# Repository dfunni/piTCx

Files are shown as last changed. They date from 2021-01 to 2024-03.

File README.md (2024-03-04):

# piTCx
piTCx is a Raspberry Pi based roaster control system using Artisan Roasterscope as front-end UI. A Raspberry Pi can interface with the piTCx Power HAT+ to record temperatures from up to four thermocouples as well as the temperature sensor (MCP9800) on the piTCx board. For roaster control, the Raspberry Pi can perform heater control using slow PWM (1 Hz) with the Artisan software providing PID control. Heater control requires a solid state relay connected to the OT1 jumper on the piTCx HAT+. The piTCx Power HAT+ can also power the host Raspberry Pi over GPIO through the 5V jumper connection.

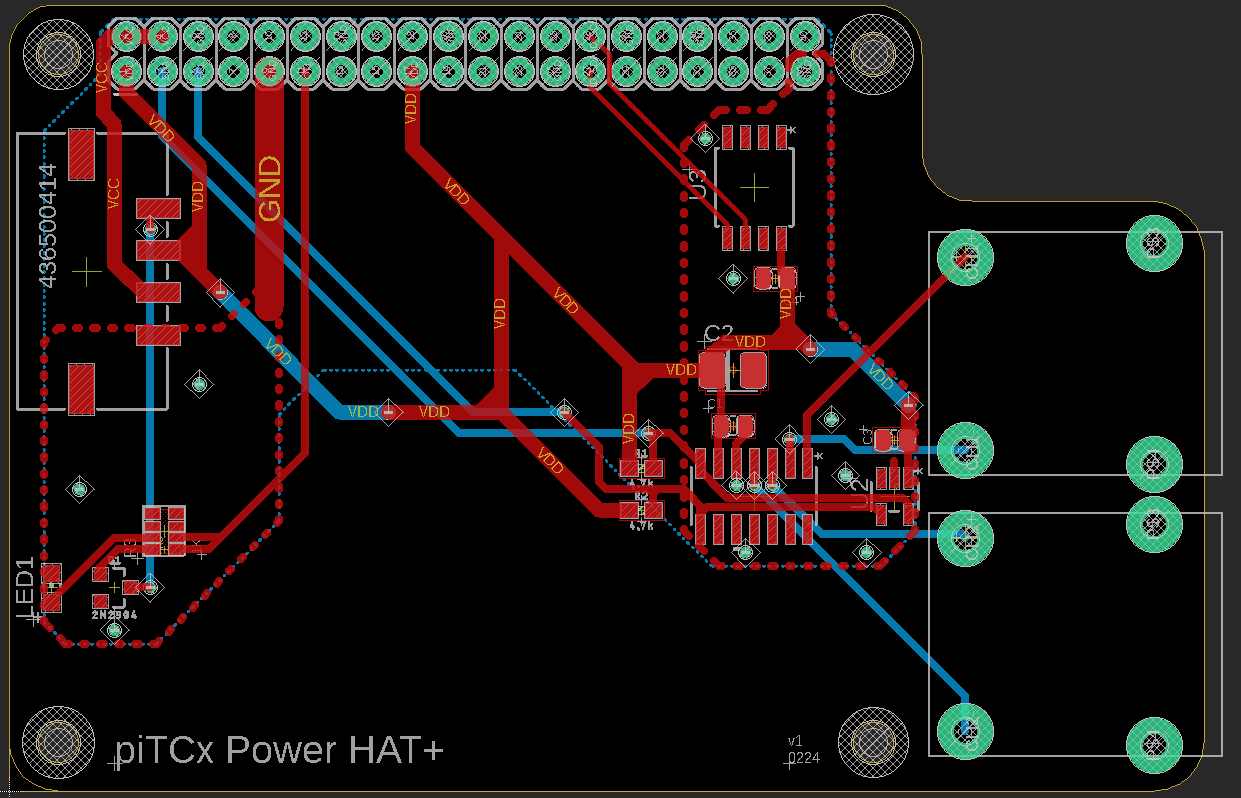
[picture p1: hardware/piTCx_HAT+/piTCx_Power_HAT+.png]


# piRoast Power
The piRoast Power is a complementary board provides  5V power to supply the Raspberry Pi via the piTCx Power HAT+. Additionally, the board contains a solid state relay for heater control.

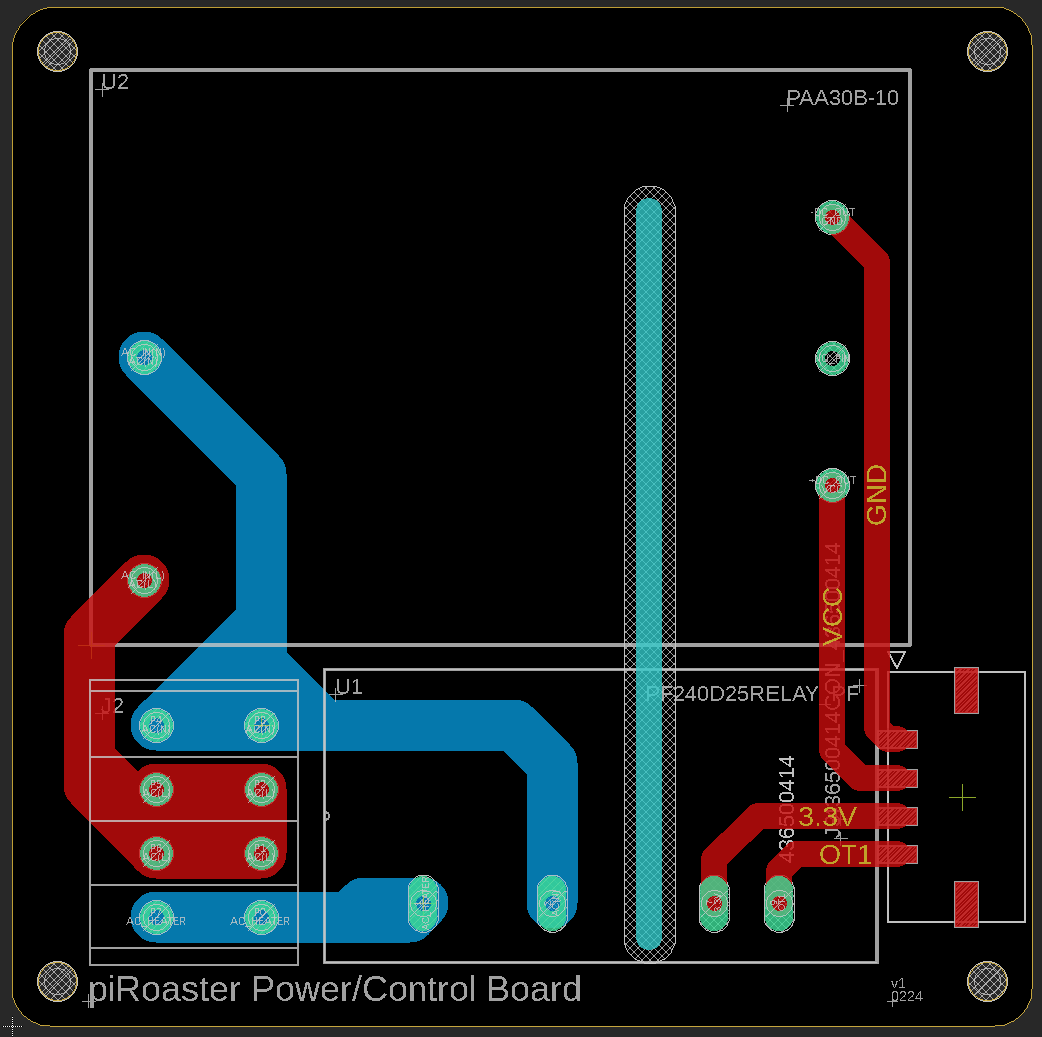
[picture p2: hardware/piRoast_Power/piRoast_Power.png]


# Raspberry Pi Setup
Starting with a fresh install of the latest raspbian OS (tested with Bookworm):

1. configure the raspi with
```
sudo raspi-config
```    
In the "Advanced" menu, select expand filesystem.

In the "Interfaces" menu enable ssh, I2C, Serial Port, and Remote GPIO.

Reboot to finish the configuration.

2. Install required tools
```
sudo apt install socat
```
3. Ensure pigpiod is enabled and running
```
sudo systemctl enable pigpiod
sudo systemctl start pigpiod
```
4. Install Artisan
```
curl -L -O https://github.com/artisan-roaster-scope/artisan/releases/download/<vx.xx.x>/<artisan-linux-x.xx.x.deb>
sudo dpkg -i <artisan-linux-x.x.x.deb>
```
5. Download and setup the piTCx code
```
git clone https://github.com/dfunni/piTCx.git
cd piTCx
python -m venv env
source env/bin/activate
pip install -r requirements.txt
```
6. Create systemd service to run the piTCx command interface. First update tcxd.service line 10 to the correct login user (e.g. pi). Then:
```
sudo cp tcxd.service /etc/systemd/system/
sudo systemctl enable tcxd.service
```
From here everything is setup and ready. The next steps are to configure Artisan for communication with the TCx board.

## (Optional) Launch Artisan on boot
Copy `start_artisan.sh` to `/etc/profile.d/` with:
```
sudo cp $HOME/piTCx/start_artisan.sh /etc/profile.d/
```
# Artisan Setup
1. Go to Config > Device
    - at the top of the ET/BT tab check Control, Curves: BT, LCDs: ET and BT
    - select TC4 radio button, set ET and BT channels, set AT Channel to None, deselect PID Firmware
    - in the Extra Devices tab add the following:
        ArduinoTC4_56; Label 1: Heater; Label 2: Fan; Curve 1: enable; Curve 2: enable
        ArduinoTC4_78; Label 1: SV; Label 2: Ambient; LCD 2: enable; Curve 1: enable; Curve 2: enable

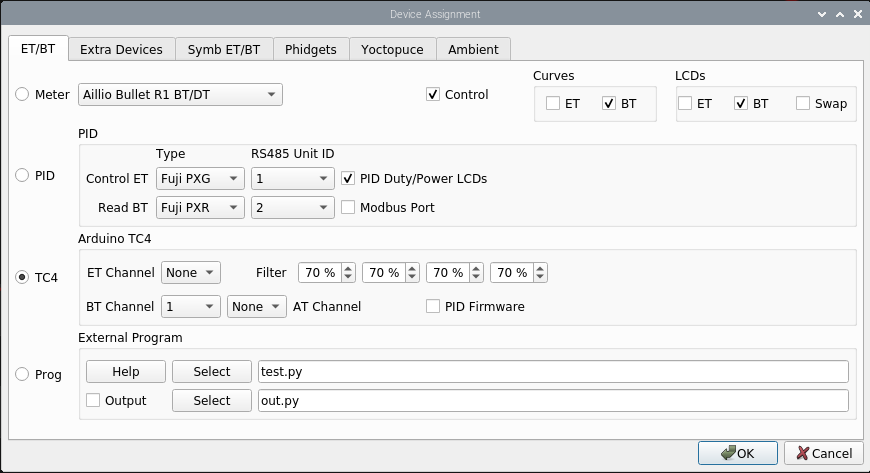
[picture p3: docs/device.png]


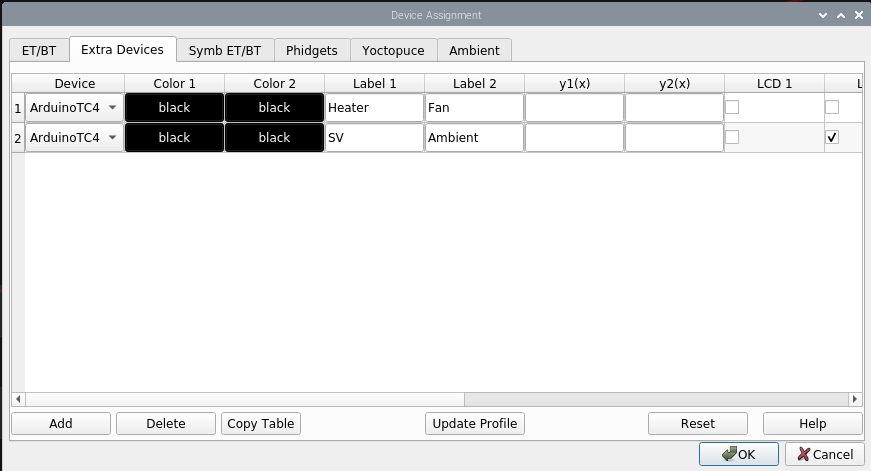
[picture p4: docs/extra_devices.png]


2. In Ports set Comm Port to /dev/ttyS91 with 115200-8-N-1 and change the serial Timeout to **0.4** seconds

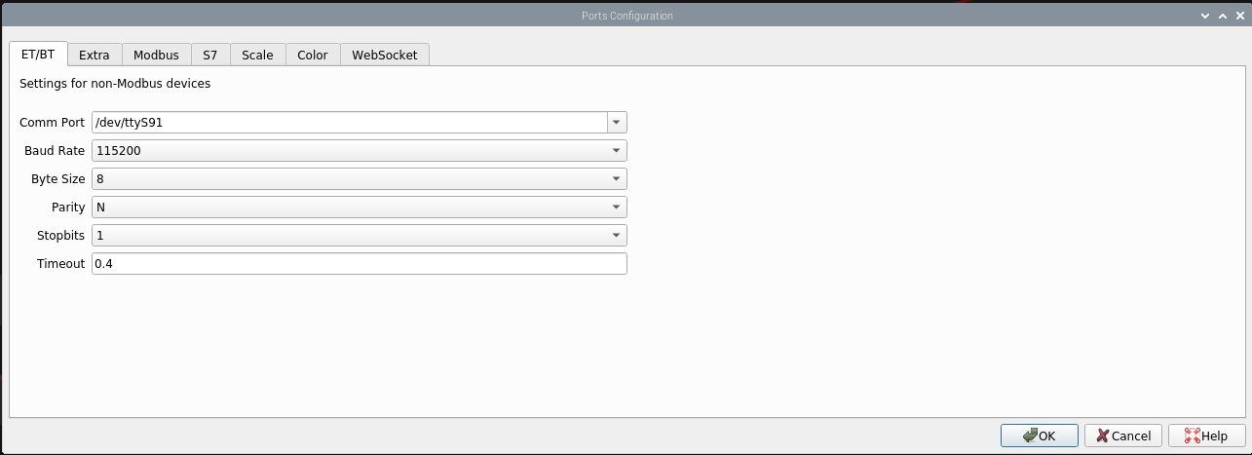
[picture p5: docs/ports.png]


3. Config > Sampling set to 1.0 seconds, accept the popup

4. Config > Curves select BT Projection and set to linear

5. Config > Events
     - set Event Types 2 to Heater and have that as the only event tyupe slected
     - set Default Buttons - DROP to Serial Command: OT1;0
     - under the Buttons Tab add the following
        Heater MAX; Type: Heater; Value: 100; Action: Serial Command; Documentation: OT1;{}
        Heater Off; Type: Heater; Value: 0; Action: Serial Command; Documentation: OT1;{}
        PID OFF; Type: Heater Value: 0; Action: Artisan Command; Documentation: PIDoff
    - Sliders - Event: Heater; Action: Serial Command; Command: OT1;{}

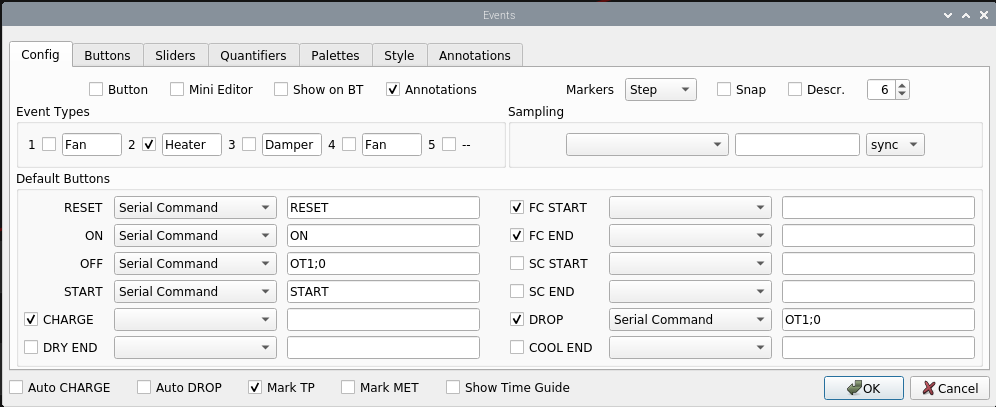
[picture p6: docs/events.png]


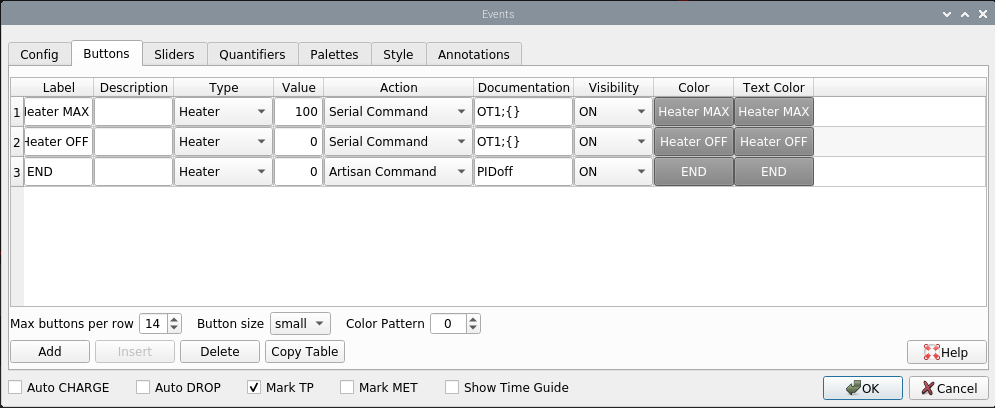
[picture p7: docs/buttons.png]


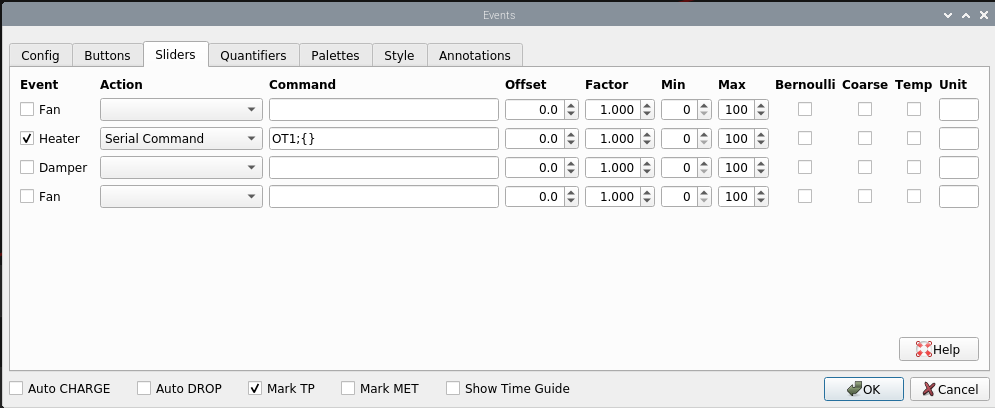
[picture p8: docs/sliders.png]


6. Config > Temperature > Celcius Mode

7. Roast > Background
    - show, BT selected
    - Load background .alog file

8. Control (Button)
    - kp: 1.30
    - ki: 0.06
    - kd: 4.50
    - Source: BT; Target - Positive: Heater; Set Value - Mode: Background; Set PID on CHARGE: enabled

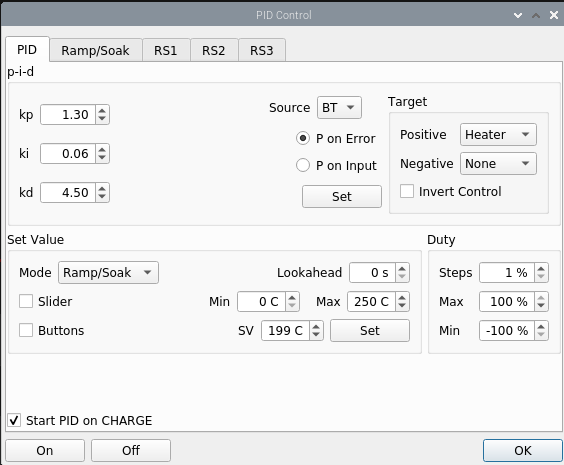
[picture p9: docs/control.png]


# Testing piTCx on Raspberry Pi
1. Ensure Raspberry Pi setup is completed per instructions in Raspberry Pi Setup
  section. Ensure piTCx HAT+ is connected.

3. In the ~/piTCx directory run pytests with:
```
cd ~/piTCx
pytest --cov
```

3. Navigate to the ~/piTCx/tests/ directory and run:
```
cd tests/
./integration_test.sh
```
Monitor the output to ensure temperatures are read, no errors are produced.

4. Run the sample rate test to ensure 1.0 second sampling intervals are working:
```
./samprate_test.sh
```
Monitor the output to esure 10 reads are taken. Check the timestamps for 1 second accuracy. 

5. Additionally, a single Artisan command can be executed with:
```
./ArtisonCMD.sh <command> [<value>]
```
 using a command value pair from the following:
| command | value | notes |
| --- | ----- | ----- |
| CHAN | 1234  | Initializes the piTCx and sets order of ADC channels |
| READ | | No value for READ command |
| UNITS | F/C | Temperature units to be read |
| OT1 | 0-100 | Sets OT1 duty cycle |
| OT2 | 0-100 | Sets OT2 duty cycle |
| IO2 | 0-100 | Sets IO2 duty cycle |

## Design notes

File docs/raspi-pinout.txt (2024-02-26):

3V3 -    3V3  (1) (2)  5V     - 5V 
SDA -  GPIO2  (3) (4)  5V     - 5V 
SCL -  GPIO3  (5) (6)  GND    - GND
--- -  GPIO4  (7) (8)  GPIO14 - ---
GND -    GND  (9) (10) GPIO15 - --- 
OT1 - GPIO17 (11) (12) GPIO18 - --- 
--- - GPIO27 (13) (14) GND    - GND
--- - GPIO22 (15) (16) GPIO23 - ---
3V3 -    3V3 (17) (18) GPIO24 - ---
--- - GPIO10 (19) (20) GND    - GND
--- -  GPIO9 (21) (22) GPIO25 - ---
--- - GPIO11 (23) (24) GPIO8  - ---
GND -    GND (25) (26) GPIO7  - ---
--- -  GPIO0 (27) (28) GPIO1  - ---
--- -  GPIO5 (29) (30) GND    - GND 
--- -  GPIO6 (31) (32) GPIO12 - ---
--- - GPIO13 (33) (34) GND    - GND 
--- - GPIO19 (35) (36) GPIO16 - ---
--- - GPIO26 (37) (38) GPIO20 - ---
GND -    GND (39) (40) GPIO21 - ---

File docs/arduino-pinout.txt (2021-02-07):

    SCL/D13  (16) (15) ~D12/MISO
        3V3  (17) (14) ~D11/MOSI
       AREF  (18) (13) ~D10       OT2
     A0/D14  (19) (12) ~D09       OT1
     A1/D15  (20) (11)  D08
     A2/D16~ (21) (10)  D07
     A3/D17~ (22) (09) ~D06
SDA  A4/D18  (23) (08) ~D05
SCL  A5/D19~ (24) (07)  D04
     A6/D20  (25) (06) ~D03       IO3
     A7/D20  (26) (05) ~D02       IO2
3v3      5V  (27) (04)  GND       GND
      RESET  (28) (03)  RESET
GND     GND  (29) (02)  RX        TX        
        VIN  (30) (01)  TX        RX

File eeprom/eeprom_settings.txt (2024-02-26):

########################################################################
# EEPROM settings text file
#
# Use eepflash tool to write to attached HAT ID EEPROM 
#
# Tools available:
#  eepmake   Parses EEPROM text file and creates binary .eep file
#  eepdump   Dumps a binary .eep file as human readable text (for debug)
#  eepflash  Write or read .eep binary image to/from HAT EEPROM
#
########################################################################

# RFC 4122 compliant UUID
product_uuid cafef870-ff07-4368-9851-c25b4d0d856a

# 16 bit product id
product_id 0x0000

# 16 bit product version
product_ver 0x0001

# ASCII vendor string  (max 255 characters)
vendor "dfunni"

# ASCII product string (max 255 characters)
product "piTCx Power HAT+"

# Which Device Tree overlay to load
dt_blob "i2c1"

custom_data "
piTCx is a Raspberry Pi based roaster control system, see https://github.com/dfunni/piTCx for details.

MIT License

Copyright (c) 2020 dfunni

Permission is hereby granted, free of charge, to any person obtaining a copy
of this software and associated documentation files (the "Software"), to deal
in the Software without restriction, including without limitation the rights
to use, copy, modify, merge, publish, distribute, sublicense, and/or sell
copies of the Software, and to permit persons to whom the Software is
furnished to do so, subject to the following conditions:

The above copyright notice and this permission notice shall be included in all
copies or substantial portions of the Software.

THE SOFTWARE IS PROVIDED "AS IS", WITHOUT WARRANTY OF ANY KIND, EXPRESS OR
IMPLIED, INCLUDING BUT NOT LIMITED TO THE WARRANTIES OF MERCHANTABILITY,
FITNESS FOR A PARTICULAR PURPOSE AND NONINFRINGEMENT. IN NO EVENT SHALL THE
AUTHORS OR COPYRIGHT HOLDERS BE LIABLE FOR ANY CLAIM, DAMAGES OR OTHER
LIABILITY, WHETHER IN AN ACTION OF CONTRACT, TORT OR OTHERWISE, ARISING FROM,
OUT OF OR IN CONNECTION WITH THE SOFTWARE OR THE USE OR OTHER DEALINGS IN THE
SOFTWARE.
\"

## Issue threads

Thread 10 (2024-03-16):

Need fan header on HAT and/or Power Board

dfunni, 2024-03-16:
Add a 4-pin fan header to board.

Threshold: provide 5V power to fan
Objective: PWM control of fan

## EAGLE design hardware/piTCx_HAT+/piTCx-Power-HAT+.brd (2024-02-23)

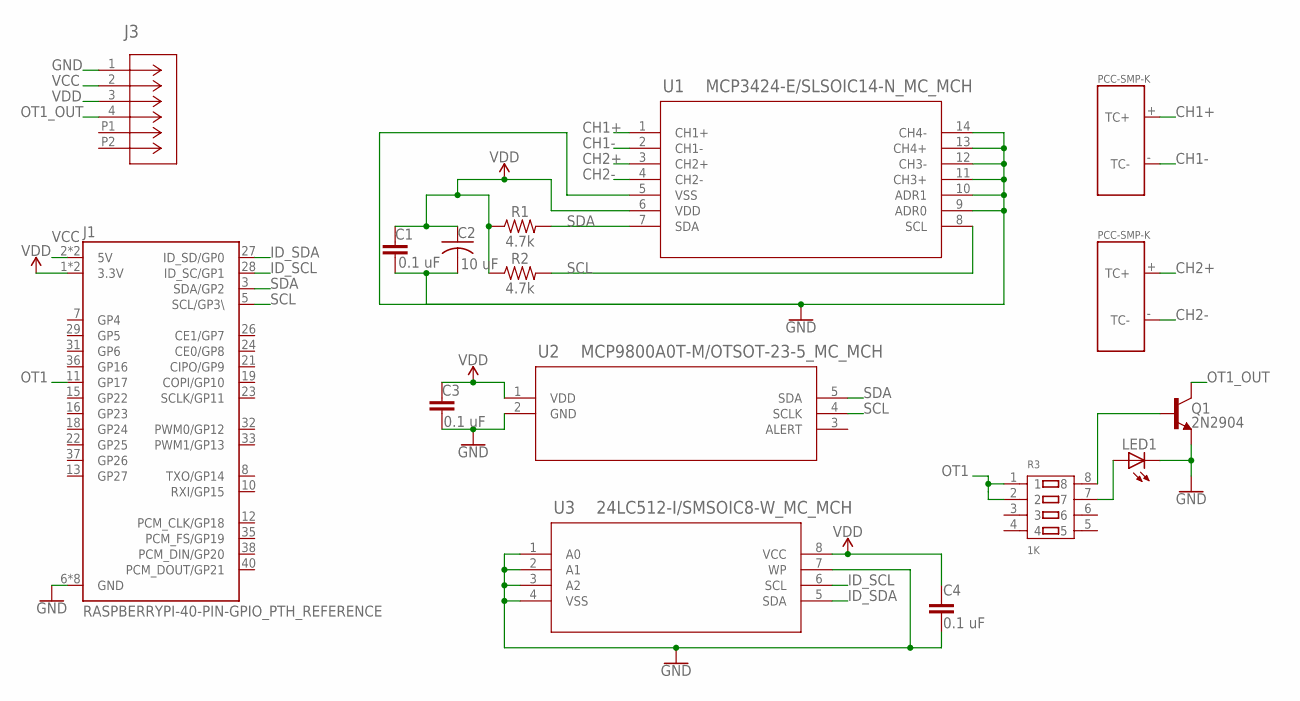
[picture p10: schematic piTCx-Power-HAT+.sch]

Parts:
C1, C3, C4: 0.1 uF; CAP_0805
C2: 10 uF; CAP_TANT_B; MPN T494A106M020AT
J1: RASPBERRYPI-40-PIN-GPIO_PTH_REFERENCE; RASPBERRY_PI_HAT_40_PIN_PTH_WITH_REFERNCE
J3: 436500414CON_436500414; CON_436500414
LED1: LEDCHIP-LED0805; CHIP-LED0805
Q1: 2N2904; SOT23-3
R1, R2: 4.7k; 0603
R3: 1K; RA1206-8
U1: MCP3424-E/SLSOIC14-N_MC_MCH; SOIC14-N_MC_MCH
U2: MCP9800A0T-M/OTSOT-23-5_MC_MCH; SOT-23-5_MC_MCH
U3: 24LC512-I/SMSOIC8-W_MC_MCH; SOIC8-W_MC_MCH
U$1, U$2: THERMOCOUPLECONN-PCC-SMP-K

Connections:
CH1+: U1.1 (CH1+), U$1.+ (TC+)
CH1-: U1.2 (CH1-), U$1.- (TC-)
CH2+: U1.3 (CH2+), U$2.+ (TC+)
CH2-: U1.4 (CH2-), U$2.- (TC-)
GND: C1.2, C2.2, C3.2, C4.2, J1.6 (GND), J1.9 (GND), J1.14 (GND), J1.20 (GND), J1.25 (GND), J1.30 (GND), J1.34 (GND), J1.39 (GND), J3.1, LED1.C, Q1.2 (E), U1.5 (VSS), U1.9 (ADR0), U1.10 (ADR1), U1.11 (CH3+), U1.12 (CH3-), U1.13 (CH4+), U1.14 (CH4-), U2.2 (GND), U3.1 (A0), U3.2 (A1), U3.3 (A2), U3.4 (VSS), U3.7 (WP)
ID_SCL: J1.28 (ID_SC/GP1), U3.6 (SCL)
ID_SDA: J1.27 (ID_SD/GP0), U3.5 (SDA)
unnamed: Q1.1 (B), R3.8
unnamed: LED1.A, R3.7
OT1: J1.11 (GP17), R3.1, R3.2
OT1_OUT: J3.4, Q1.3 (C)
SCL: J1.5 (SCL/GP3\), R2.2, U1.8 (SCL), U2.4 (SCLK)
SDA: J1.3 (SDA/GP2), R1.2, U1.7 (SDA), U2.5 (SDA)
VCC: J1.2 (5V), J1.4 (5V), J3.2
VDD: C1.1, C2.1, C3.1, C4.1, J1.1 (3.3V), J1.17 (3.3V), J3.3, R1.1, R2.1, U1.6 (VDD), U2.1 (VDD), U3.8 (VCC)

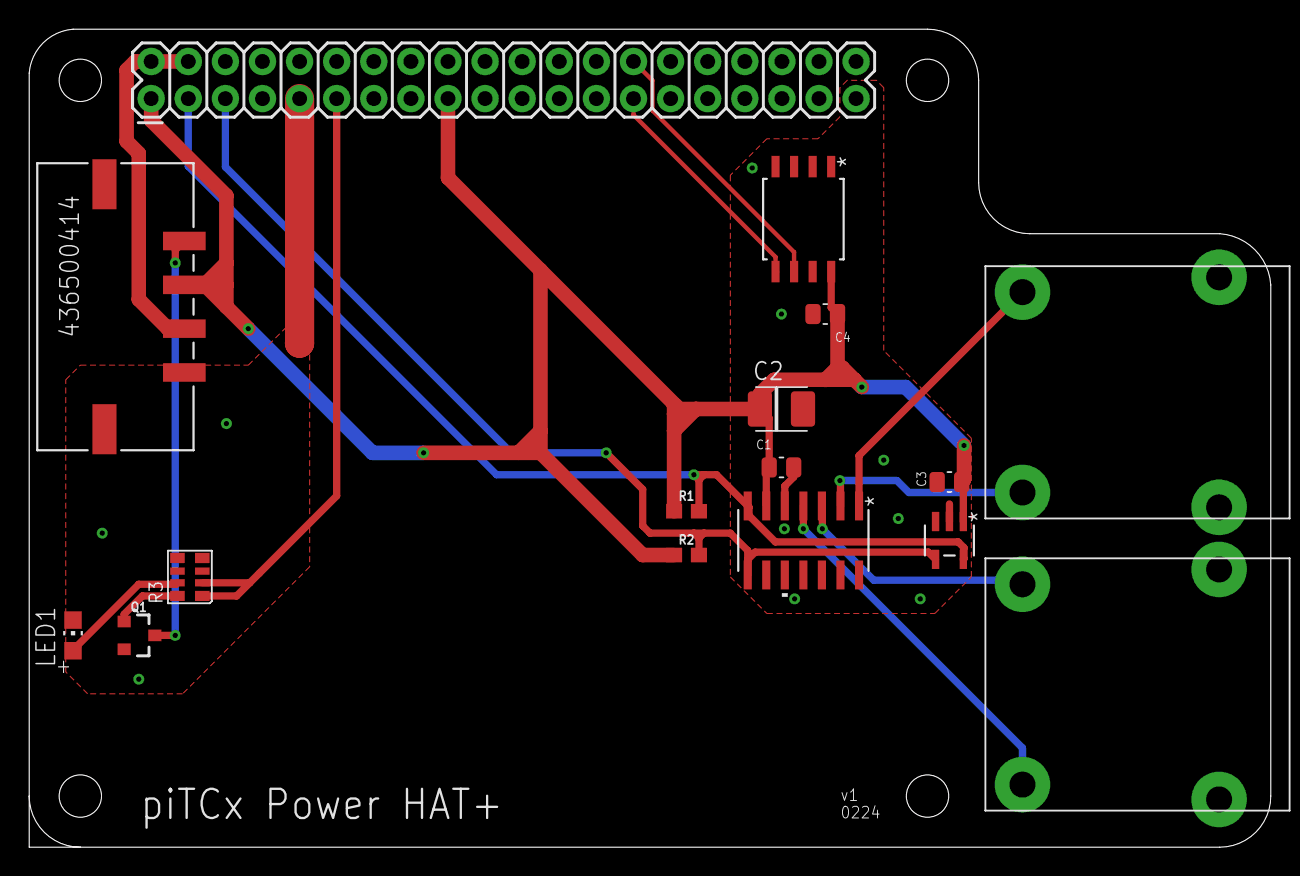
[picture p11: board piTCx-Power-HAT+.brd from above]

Board: 2 copper layers, 85.0 x 56.0 mm, 16 parts (0 on the bottom side), 15 nets.

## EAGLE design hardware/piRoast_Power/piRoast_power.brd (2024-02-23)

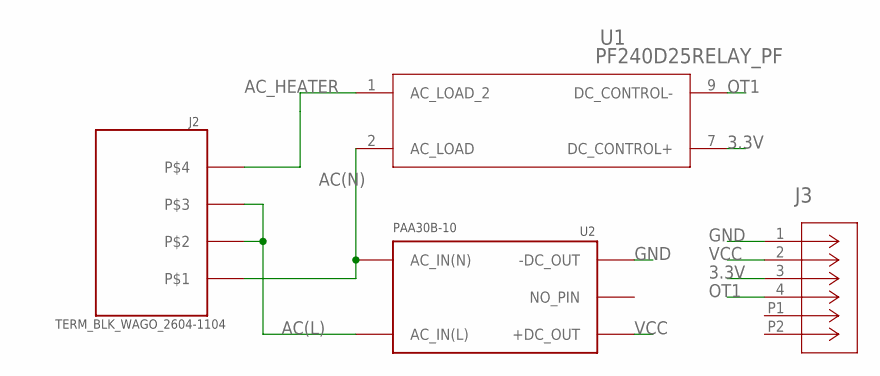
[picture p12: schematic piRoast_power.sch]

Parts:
J2: TERM_BLK_WAGO_2604-1104
J3: 436500414CON_436500414; CON_436500414
U1: PF240D25RELAY_PF; RELAY_PF
U2: PAA30B-10

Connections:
3.3V: J3.3, U1.7 (DC_CONTROL+)
AC(L): J2.P1, J2.P2, J2.P5, J2.P6, U2.AC_IN(L)
AC(N): J2.P3, J2.P4, U1.2 (AC_LOAD), U2.AC_IN(N)
AC_HEATER: J2.P0, J2.P7, U1.1 (AC_LOAD_2)
GND: J3.1, U2.-DC_OUT
OT1: J3.4, U1.9 (DC_CONTROL-)
VCC: J3.2, U2.+DC_OUT

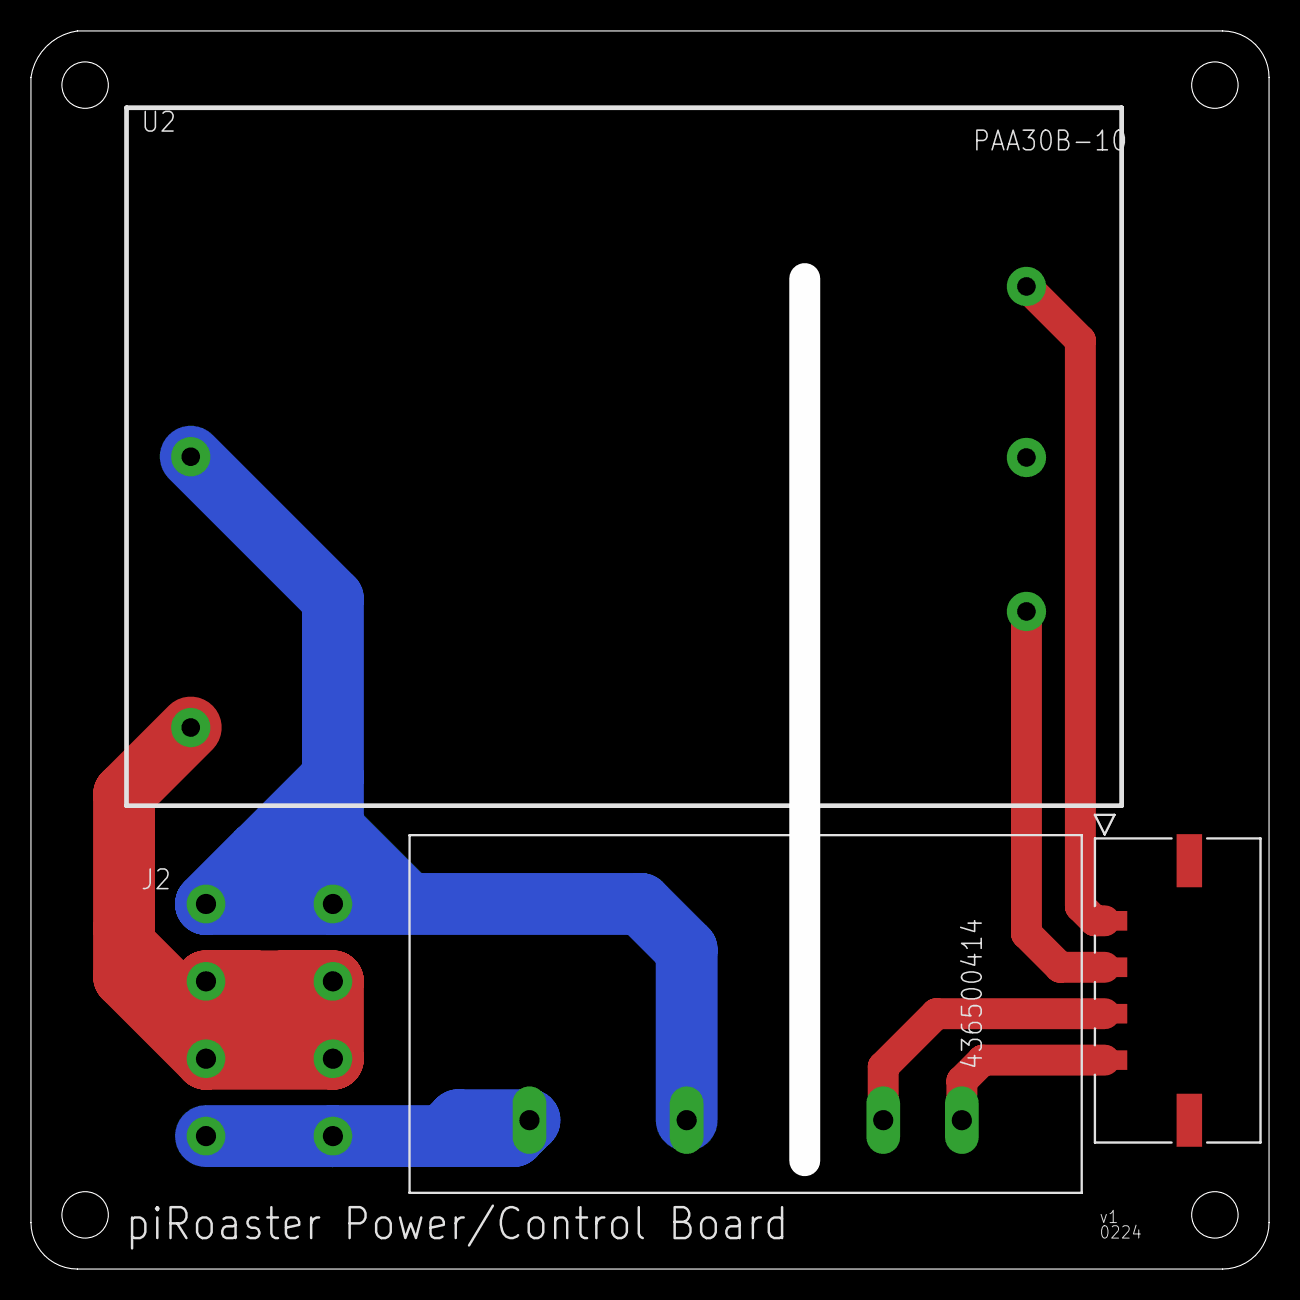
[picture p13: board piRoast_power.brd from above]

Board: 2 copper layers, 80.0 x 80.0 mm, 4 parts (0 on the bottom side), 7 nets.

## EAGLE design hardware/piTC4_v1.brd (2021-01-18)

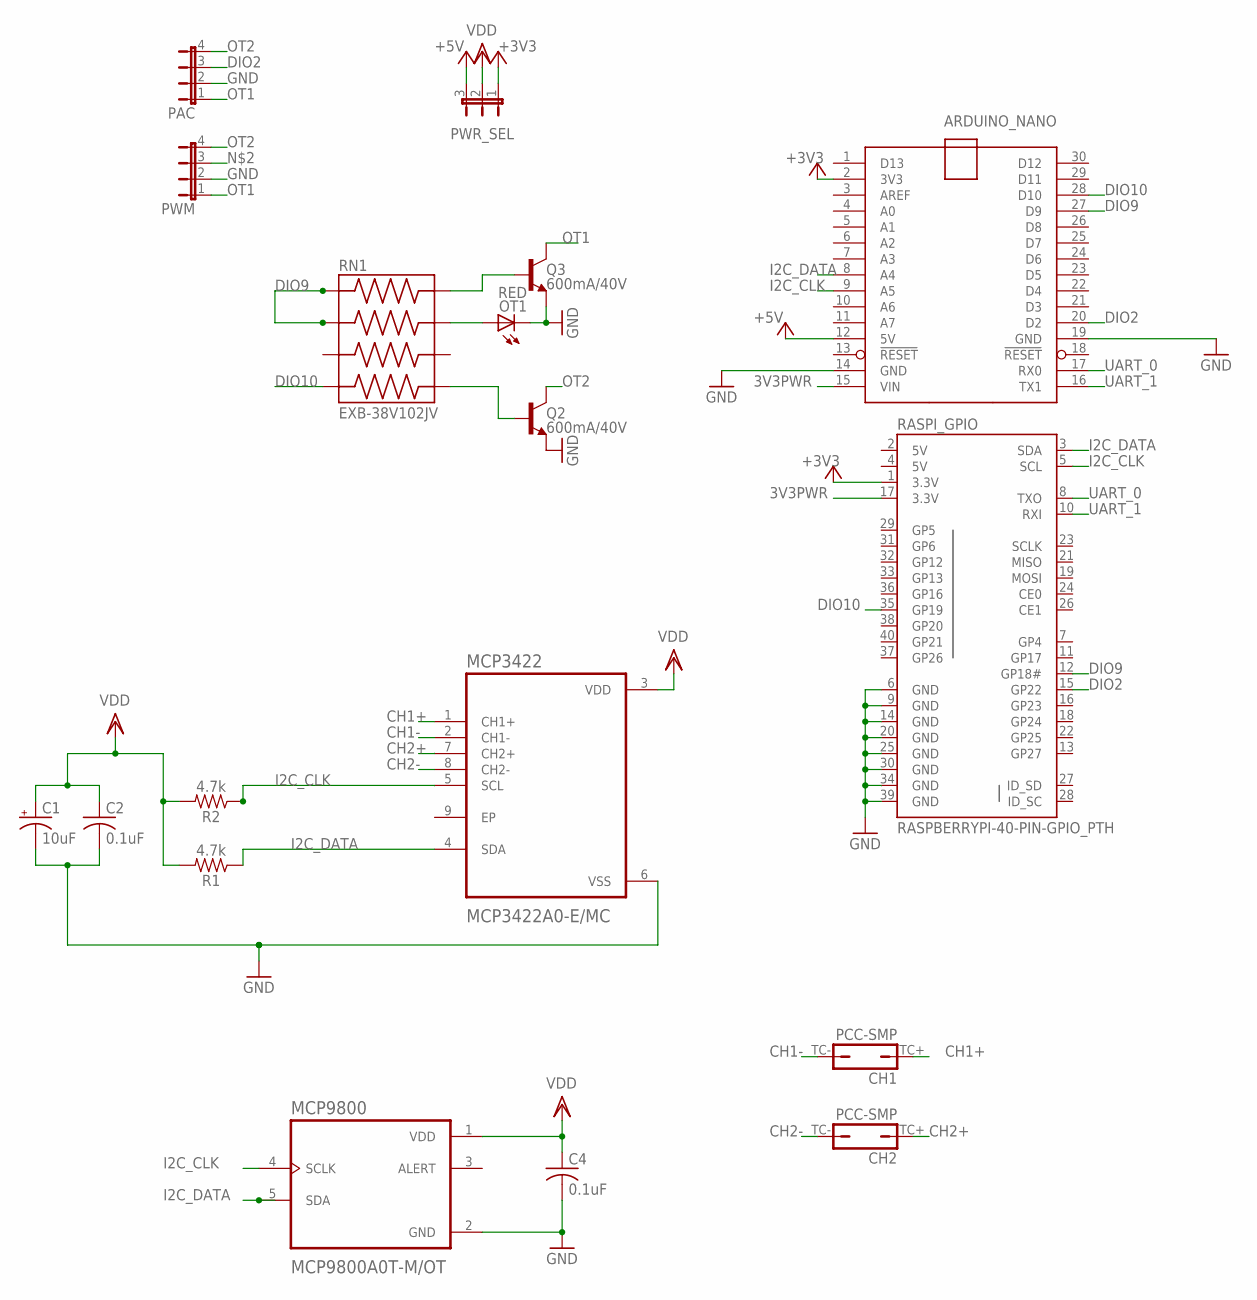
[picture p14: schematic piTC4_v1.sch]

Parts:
ARDUINO_NANO: ARDUINO_NANO
C1: 10uF; EIA3216
C2, C4: 0.1uF; C0805
CH1, CH2: PCC-SMP
MCP3422: MCP3422A0-E/MC; SON50P200X300X100-9N
MCP9800: MCP9800A0T-M/OT; SOT95P270X145-5N
OT1: RED; CHIPLED_0805
PAC: JP4E; JP4
PWM: JP4E; JP4
PWR_SEL: JP2E; JP2
Q2, Q3: 600mA/40V; SOT23-3
R1, R2: 4.7k; 0603
RASPI_GPIO: RASPBERRYPI-40-PIN-GPIO_PTH; 2X20_SHROUDED
RN1: EXB-38V102JV; RESCAXS80P320X160X60-8N

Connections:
3V3PWR: ARDUINO_NANO.15 (VIN), RASPI_GPIO.17 (3.3V)
5V: RASPI_GPIO.2 (5V), RASPI_GPIO.4 (5V)
+3V3: ARDUINO_NANO.2 (3V3), PWR_SEL.1, RASPI_GPIO.1 (3.3V)
+5V: ARDUINO_NANO.12 (5V), PWR_SEL.3
CH1+: CH1.TC+ (1), MCP3422.1 (CH1+)
CH1-: CH1.TC- (2), MCP3422.2 (CH1-)
CH2+: CH2.TC+ (1), MCP3422.7 (CH2+)
CH2-: CH2.TC- (2), MCP3422.8 (CH2-)
DIO2: ARDUINO_NANO.20 (D2), PAC.3, RASPI_GPIO.15 (GP22)
DIO9: ARDUINO_NANO.27 (D9), RASPI_GPIO.12 (GP18#), RN1.1, RN1.2
DIO10: ARDUINO_NANO.28 (D10), RASPI_GPIO.35 (GP19), RN1.4
GND: ARDUINO_NANO.14 (GND), ARDUINO_NANO.19 (GND), C1.-, C2.2, C4.2, MCP3422.6 (VSS), MCP9800.2 (GND), OT1.C, PAC.2, PWM.2, Q2.2 (E), Q3.2 (E), RASPI_GPIO.6 (GND), RASPI_GPIO.9 (GND), RASPI_GPIO.14 (GND), RASPI_GPIO.20 (GND), RASPI_GPIO.25 (GND), RASPI_GPIO.30 (GND), RASPI_GPIO.34 (GND), RASPI_GPIO.39 (GND)
I2C_CLK: ARDUINO_NANO.9 (A5), MCP3422.5 (SCL), MCP9800.4 (SCLK), R2.1, RASPI_GPIO.5 (SCL)
I2C_DATA: ARDUINO_NANO.8 (A4), MCP3422.4 (SDA), MCP9800.5 (SDA), R1.1, RASPI_GPIO.3 (SDA)
unnamed: Q2.1 (B), RN1.5
unnamed: Q3.1 (B), RN1.8
unnamed: OT1.A, RN1.7
OT1: PAC.1, PWM.1, Q3.3 (C)
OT2: PAC.4, PWM.4, Q2.3 (C)
UART_0: ARDUINO_NANO.17 (RX0), RASPI_GPIO.8 (TXO)
UART_1: ARDUINO_NANO.16 (TX1), RASPI_GPIO.10 (RXI)
VDD: C1.+, C2.1, C4.1, MCP3422.3 (VDD), MCP9800.1 (VDD), PWR_SEL.2, R1.2, R2.2

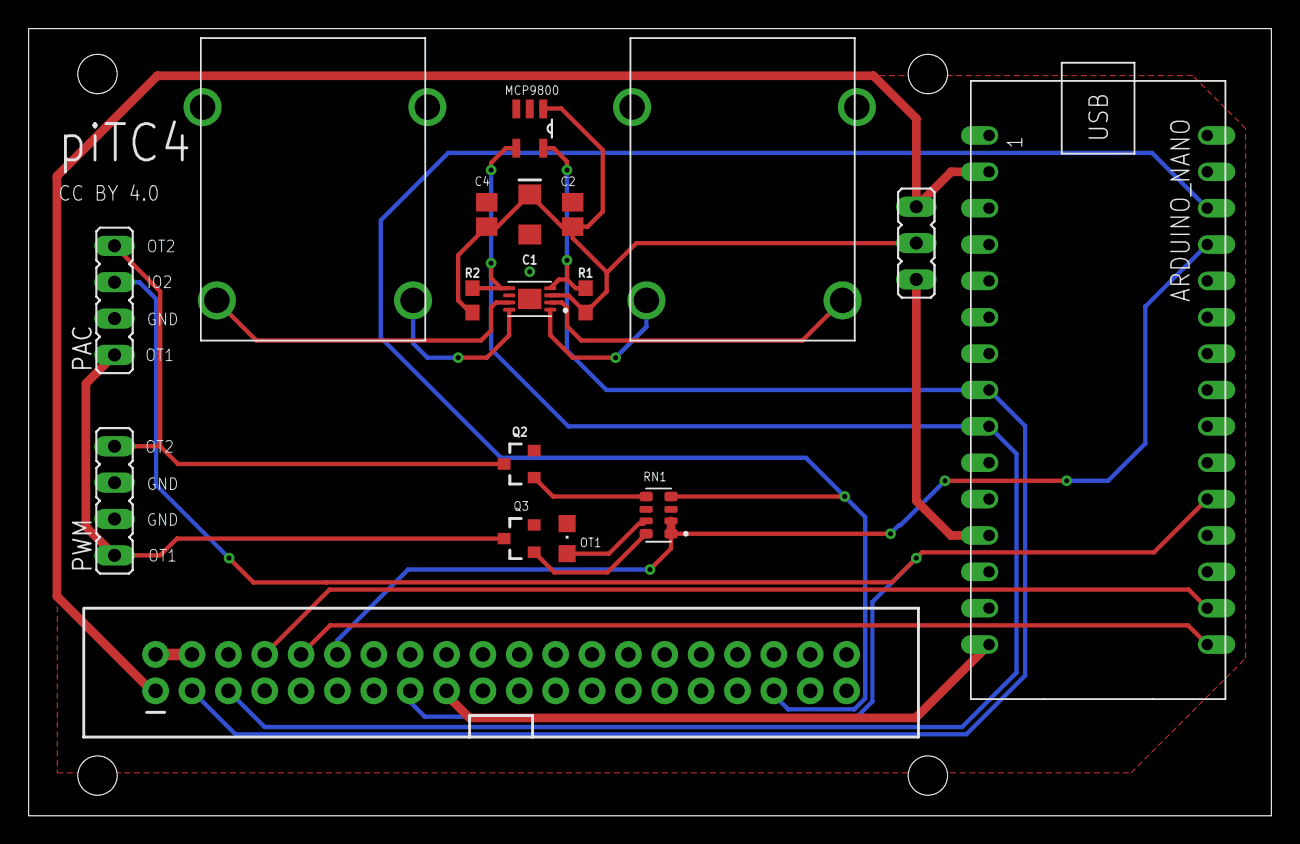
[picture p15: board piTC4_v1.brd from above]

Board: 2 copper layers, 86.8 x 55.0 mm, 18 parts (0 on the bottom side), 22 nets.

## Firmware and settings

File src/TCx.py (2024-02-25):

import logging
import sys
import serial
import yaml
from argparse import ArgumentParser

import smbus2 as smbus

from gpiozero import PWMOutputDevice
from gpiozero.pins.pigpio import PiGPIOFactory

from devices import MCP9800
from devices import TC
from utils import read_temps

logger = logging.getLogger(__name__)

class TCx(object):
    """This is a class for the TCx Raspberry Pi HAT.
    """

    def __init__(self, serial_bus, config):
        """Initializes the TCx instance based on serial bus used.

        Args:
            serial_bus (serial.Serial): Defines the main communication bus.

        """

        # ADC Setup
        self.serial_bus = serial_bus
        self.i2c_bus = smbus.SMBus(bus=1)  # I2C bus 1 is always used with GPIO

        self.amb = MCP9800(bus=self.i2c_bus)
        # self.c0 = MCP342x(bus=self.i2c_bus, chan=0, tc_type='k_type', res=16)
        # self.c1 = MCP342x(bus=self.i2c_bus, chan=1, tc_type='k_type', res=16)
        # # channels 2 and 3 only used for MCP3424
        # self.c2 = MCP342x(bus=self.i2c_bus, chan=2, tc_type='k_type', res=16)
        # self.c3 = MCP342x(bus=self.i2c_bus, chan=3, tc_type='k_type', res=16)
        
        self.device_dict = {'amb': self.amb,
                            'tcs': []}

        self.handler_dict = {'READ': self.handle_read,
                             'CHAN': self.handle_chan,
                             'UNITS': self.handle_units,
                             'OT1': self.handle_ot1,
                             'OT2': self.handle_ot2,
                             'IO2': self.handle_io2,
                             'FILT': self.handle_filt,
                             'BUTTON': self.handle_button,
                             }

        self.units = "C"  # temperature units
        self.isinit = False  # ensure CHAN before READ

        # GPIO setup
        pins = config['PIN_CONFIG']
        factory = PiGPIOFactory()
        self.ot1 = PWMOutputDevice(pin=pins['pOT1'], pin_factory=factory)
        # the following interfaces are unused but kept for TC4 compatability
        self.ot2 = PWMOutputDevice(pin=pins['pOT2'], pin_factory=factory)
        self.io2 = PWMOutputDevice(pin=pins['pIO2'], pin_factory=factory)

        self.heater_duty = 0
        self.fan_duty = 100  # assumption that fan is on to start
        self.dc_fan_duty = 0

        # variables for filter
        self.filt = [0] * 4
        self.prev_temps = [0] * 4
        self.cmd = None  # initialize
        # self.chan_idx = []  # initialize

    def decode_command(self, cmd):
        '''Parses Artisan commands and takes appropriate action
        '''
        cmd = cmd.decode('utf-8').replace('\n', '')
        self.cmd = str(cmd).split(';')
        logger.debug('%s', self.cmd)
        _ = self.handler_dict.get(self.cmd[0], self.handle_unknown)()

    def handle_read(self):
        '''Reads thermocouple temps and sends output over serial
        Command of type: READ
        '''
        if self.isinit:
            T_Cs, T_Fs = read_temps(self.device_dict)
            logger.debug('%s', T_Cs)
            Ts = T_Fs if self.units == 'F' else T_Cs
            Ts = self.dofilter(Ts)
            AT = Ts[0]
            if len(Ts[1:]) == 1:
                Ts.append(0.0)
            T_str = ','.join([f'{T}' for T in Ts[1:]])
            HT = self.heater_duty
            FN = self.fan_duty
            SV = 0
            msg = f'{AT},{T_str},{HT},{FN},{SV}'
            self.serial_bus.write(bytes(msg, 'ascii'))
            logger.info('%s: %s', self.cmd, msg)
        else:  # if CHAN command has not been read yet
            logger.warning("READ before CHAN command")

    def handle_filt(self):
        '''Sets the filter values to a list of floats between 0 and 1
        Command of type: FILT;70;70;70;70
        '''
        filts = str(self.cmd[1]).split(',')
        self.filt = [int(i)/100.0 for i in filts]
        logger.info('%s:%s', self.cmd, self.filt)

    def handle_chan(self):
        '''Initializes TC4, sets up channels for ET and BT
        Command of type: CHAN;1234

        - A 0 index means there is no channel assigned to that value.
        - If Arduino_34 is not set the last two values will be 0 and we should
        omit them from chans.
        - Channel values from the command are reduced by one to index the
        proper ADC channel.
        Examples:
        CHAN;0100 results from ET: None, BT: ADC channel 0, Arduino_34 off
        CHAN;2134 results from ET: ADC channel 1, BT channel 0, Arduino_34 on
        '''
        self.isinit = True
        chans = self.cmd[1]
        # truncate unused channels if artisan setup with no ArduinoTC4_34
        if chans[2:] == '00':
            chans = chans[:2]
        chan_setup = [int(i)-1 if i != '0' else None for i in chans]  # list of ints
        
        logger.debug('%s', chan_setup)
        # instantiate thermocouples
        self.device_dict['tcs'] = [None if ch == None else TC(self.i2c_bus, ch) for ch in chan_setup]
        logger.info(self.device_dict['tcs'])
        logger.info('%s', self.cmd)
        self.serial_bus.write(b'#')
        self.handle_read()

    def handle_units(self):
        '''Sets temperature units.
        Command of type: UNITS;C
        '''
        self.units = self.cmd[1]
        logger.info('%s:%s', self.cmd, self.units)

    def handle_ot1(self):
        '''Slow PWM eater control, 1 Hz
        COmmand of type: OT1;100
        '''
        self.heater_duty = self.cmd[1]
        duty = float(self.heater_duty) / 100.0
        if duty == 0:
            self.ot1.off()
        elif duty == 1:
            self.ot1.on()
        else:
            self.ot1.blink(on_time=duty, off_time=(1-duty), n=None)
        logger.info('%s:%s', self.cmd, self.heater_duty)

    def handle_ot2(self):
        '''PWM AC fan cotrol, ZCD at IO2
        Command of type: OT2;100
        '''
        self.fan_duty = self.cmd[1]
        duty = float(self.fan_duty) / 100.0
        self.ot2.blink(on_time=duty, off_time=(1-duty), n=None)
        if duty == 0:
            self.ot2.off()
        elif duty == 1:
            self.ot2.on()
        else:
            self.ot2.blink(on_time=duty, off_time=(1-duty), n=None)
        logger.info('%s:%s', self.cmd, self.fan_duty)

    def handle_io2(self):
        '''For ZCD, TODO'''
        self.dc_fan_duty = self.cmd[1]
        duty = float(self.dc_fan_duty) / 100.0
        self.io2.blink(on_time=duty, off_time=(1-duty), n=None)
        if duty == 0:
            self.io2.off()
        elif duty == 1:
            self.io2.on()
        else:
            self.io2.blink(on_time=duty, off_time=(1-duty), n=None)
        logger.info('%s:%s', self.cmd, self.dc_fan_duty)

    def handle_button(self):
        '''Log Artisan button presses
        Command of type: BUTTON;START
        '''
        logger.info(self.cmd)

    def handle_unknown(self):
        '''All other commands'''
        logger.warning('%s is not implemented yet', self.cmd)

    def dofilter(self, temps):
        '''Simple IIR filter over all temperatures read:
                y[k] = y[k-1]*f - x[k]*(1-f)
        where f is the filter value between 0 and 1
        '''
        amb = temps[0]
        temps = temps[1:]
        self.prev_temps = self.prev_temps[:len(temps)]
        self.filt = self.filt[:len(temps)]
        tmp = [self.prev_temps[i]*self.filt[i] for i, temp in enumerate(temps)]
        y = [round(tmp[i] + temp*(1-self.filt[i]), 4) for i, temp in enumerate(temps)]
        self.prev_temps = y
        return [amb] + y


if __name__ == '__main__':
    parser = ArgumentParser(description="Handles interfaces for TCx hardware.")
    ArgumentParser()
    parser.add_argument('user', metavar='USER', type=str,
                        help='the user where TCx code is located')
    args = parser.parse_args()
    with open(f"/home/{args.user}/piTCx/config.yml", 'r',
              encoding="utf-8") as ymlfile:
        config = yaml.load(ymlfile, Loader=yaml.FullLoader)
    logging.basicConfig(filename=config['LOG_FILE'],
                        format=config['LOG_FORMAT'],
                        datefmt=config['LOG_DATEFMT'],
                        level=config['LOG_LEVEL'])
    with serial.Serial('/dev/ttyS90', 115200) as ser:
        tcx = TCx(ser, config)

        while True:
            try:
                command = ser.readline()
                logger.debug(command)
                tcx.decode_command(command)
            except KeyboardInterrupt:
                sys.exit()

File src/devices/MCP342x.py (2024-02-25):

import logging
import time
import smbus2 as smbus

logger = logging.getLogger(__name__)


class MCP342x(object):
    """Class to represent a single MCP342x ADC channel.

        configuration register:
                    x x x x x x x x
                    | [_] | [_] [_]
        not ready __/  |  |  |   |
        channel _______/  |  |   |
        mode _____________/  |   |
        resolution __________/   |
        gain ____________________/

        not ready: 1=output not updated, 0=output reg has updated value
        channel: 00 = channel 1 (default)
                 01 = channel 2
                 10 = channel 3 MCP3424 only, treated as “00” by MCP3422/3
                 11 = channel 4 MCP3424 only, treated as “01” by MCP3422/3
        mode: 1=continuous converstion (default), 0=one-shot mode
        resolution: 00 = 12bit / 240 SPS (default)
                    01 = 14bit / 60 SPS
                    10 = 16bit / 15 SPS
                    11 = 18bit / 3.75 SPS
        gain: 00=x1 (default)
              01=x2
              10=x4
              11=x8
    """
    SHIFT_NRDY = 7
    SHIFT_CHAN = 5
    SHIFT_MODE = 4
    SHIFT_RSLN = 2
    SHIFT_GAIN = 0

    mode_map = {'continuous': 0b1,
                'oneshot': 0b0}

    rsln_map = {12: 0b00,
                14: 0b01,
                16: 0b10,
                18: 0b11}

    gain_map = {1: 0b00,
                2: 0b01,
                4: 0b10,
                8: 0b11}

    lsb_map = {12: 1e-3,
               14: 250e-6,
               16: 62.5e-6,
               18: 15.625e-6}

    nbytes_map = {12: 3,
                  14: 3,
                  16: 3,
                  18: 4}

    convert_map = {12: 1.0/240,
                   14: 1.0/60,
                   16: 1.0/15,
                   18: 1.0/3.75}

    def __init__(self,
                 bus,
                 address=0x68,
                 chan=0b00,
                 res=16,
                 pga=8):

        self.bus = bus
        self.address = address
        self.res = res
        self.pga = pga
        
        self.nrdy = 0b0 << self.SHIFT_NRDY
        self.chan = chan << self.SHIFT_CHAN
        self.mode = 0b0 << self.SHIFT_MODE  # initialize to one-shot
        self.rsln = self.rsln_map.get(res, 16) << self.SHIFT_RSLN
        self.gain = self.gain_map.get(pga, 8) << self.SHIFT_GAIN

        self.no_io = False
        self.configure('init')
        
        self.lsb = self.lsb_map.get(res, 16)
        self.nbytes = self.nbytes_map.get(res, 16)
        self.convert_time = self.convert_map.get(res, 16)

    def __repr__(self):
        """Representation of the class showing the address and channel
        """
        addr = hex(self.address)
        chan = self.chan >> self.SHIFT_CHAN
        return f'{type(self).__name__}: address={addr}, chan={chan}'

    def configure(self, src):
        """Set the configuration register.
        """
        self.config = self.nrdy | self.chan | self.mode | self.rsln | self.gain
        logger.debug('%s: %s %s',
                     hex(self.address), src, format(self.config, '#010b'))
        try:
            self.bus.write_byte(self.address, self.config)
            logger.debug('%s-%s', src, format(self.config, '#010b'))
        except IOError:
            logger.warning('%s', "I2C bus issue, setting temps to 0")
            self.no_io = True

    def convert(self):
        """Run one-shot temperature reading.
        """
        # No effect in continuous mode, initiates conversion in oneshot mode
        nrdy = 0b1 << self.SHIFT_NRDY
        config = nrdy | self.chan | self.mode | self.rsln | self.gain
        logger.debug('configuring %s: convert %s',
                     hex(self.address), format(config, '#010b'))
        self.bus.write_byte(self.address, config)

    def set_chan(self, chan):
        """Set the channel in the config register.
        """
        assert chan in [0, 1, 2, 3], 'invalid channel specified'
        self.chan = chan << self.SHIFT_CHAN
        self.configure('chan')

    def set_mode(self, mode):
        """Set the mode in the config register.
        """
        self.mode = self.mode_map.get(mode, 'oneshot') << self.SHIFT_MODE
        self.configure('mode')

    def set_rsln(self, rsln):
        """Set the resolution in the config register
        """
        self.rsln = self.rsln_map.get(rsln, 18) << self.SHIFT_RSLN
        self.lsb = self.lsb_map.get(rsln, 18)
        self.nbytes = self.nbytes_map.get(rsln, 18)
        self.convert_time = self.convert_map.get(rsln, 18)
        self.res = rsln
        self.configure('rsln')

    def set_gain(self, pga):
        """Set the gain in the config regitster
        """
        self.pga = pga
        self.gain = self.gain_map.get(pga, 8) << self.SHIFT_GAIN
        self.configure('gain')

    def raw_read(self):
        """Monitor bus until conversion is done, then read raw.
        """
        while True:
            d = self.bus.read_i2c_block_data(self.address,
                                             self.config,
                                             self.nbytes)
            config_used = d[-1]
            if (config_used & 0b10000000) == 0:  # conversion complete
                count = 0
                for i in range(self.nbytes - 1):  # read data not config
                    count <<= 8
                    count |= d[i]
                sign_bit_mask = 1 << (self.res - 1)
                count_mask = sign_bit_mask - 1
                sign_bit = count & sign_bit_mask
                count &= count_mask
                if sign_bit:
                    count = -(~count & count_mask) - 1
                logger.debug('count: %s, sign_bit: %s',
                             bin(count), bin(sign_bit))
                return count, config_used

    def read(self, raw=False):
        """Convert the raw count to a voltage reading.
        """
        count, config_used = self.raw_read()
        if config_used != self.config:
            c1 = bin(config_used)
            c2 = bin(self.config)
            logging.error('configuration error: %s != %s', c1, c2)
            return -1
        if raw:
            return count
        voltage = count * self.lsb / self.pga
        return voltage

    def convert_and_read(self, samples=None, **kwargs):
        """Runs one-shot conversion and reads values.
        """
        if self.no_io:
            return ([.01] if samples is None else [.01]*samples)
        if samples is not None:
            r = [0] * samples
        for sn in ([0] if samples is None else range(samples)):
            self.convert()
            time.sleep(0.95 * self.convert_time)
            val = self.read(**kwargs)
            if samples is not None:
                r[sn] = val
            else:
                r = val
        return r
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

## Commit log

2021-01-02 code to read thermocouple and ambient temperature over I2C
2021-01-03 cleaned up device drivers
2021-01-03 updated test script for new drivers
2021-01-04 moved temperature conversion utils to thermocouple.py
2021-01-06 modified device drivers, added artisan communication code
    [options.csv]
2021-01-11 added 1Hz pwm control of OT1
    [options.csv]
2021-01-11 corrected pins
    [options.csv]
2021-01-18 initial commit of hardware and updated docs
    [TC4nano_v4.brd, TC4nano_v4.sch, options.csv]
2021-01-18 renamed hardware files
    [piTC4_v1.brd, piTC4_v1.sch]
2021-01-21 renamed files
    [IO-configs.csv]
2021-01-21 updated hardware
    [RM_htr.brd, RM_htr.sch, TCduo_v1.brd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]
2021-02-07 added arduino pinout
2021-02-10 added filter handling
2021-03-07 added Artisan Button handeling
2021-03-28 added handling of charge button
2023-12-19 sample interval bug fix
    [TCx.py, thermocouple.py]
2023-12-20 changed ADC resolution to 16 bit
2024-02-23 HAT+ hardware v1 updates
    [RM_htr.brd, RM_htr.sch, TCduo_v1.brd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]
2024-03-14 corrected PID settings in artisan

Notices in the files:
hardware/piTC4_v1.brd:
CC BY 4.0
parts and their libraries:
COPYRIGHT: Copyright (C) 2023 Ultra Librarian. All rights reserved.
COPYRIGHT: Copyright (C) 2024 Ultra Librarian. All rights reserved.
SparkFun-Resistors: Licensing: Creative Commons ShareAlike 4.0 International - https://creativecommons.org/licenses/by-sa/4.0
